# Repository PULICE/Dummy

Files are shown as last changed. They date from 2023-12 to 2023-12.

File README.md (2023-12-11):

# Dummy
稚晖君dummy复制，目标是全国产谐波减速器本仓库继承自https://gitee.com/switchpi/dummy.git

1. 目录描述
- Firmware 包括ref控制板，42，35驱动板所用源代码
- Hardware 重新设计包括ref控制板，42，35驱动板schematic, pcb所有文件
- 3d-model 所有复制dummy 3d打印文件
- ESP32-iot esp32 supports files

1. 重新设计的ref控制板
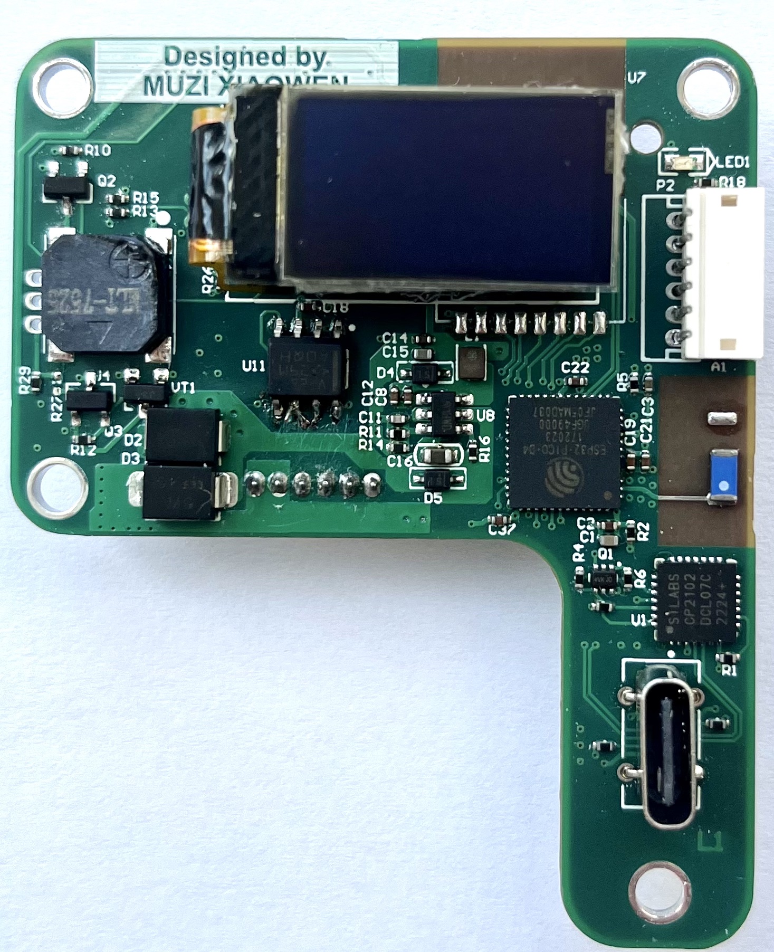
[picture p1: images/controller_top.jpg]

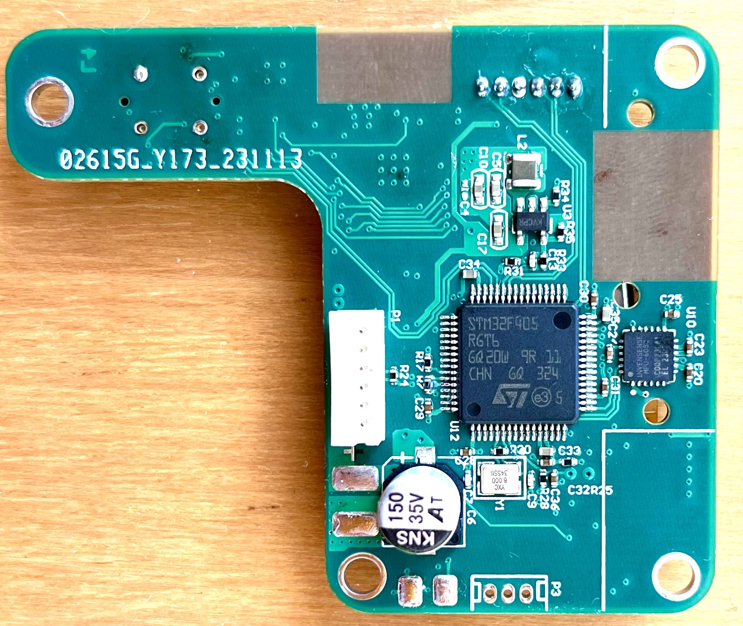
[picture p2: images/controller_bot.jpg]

- 简化设计，更适合量产
1. 修改所有1.0mm的连接器为插针1.5mm，fix原版连接器容易脱落
1. 删除base板，将base板子集成到了主板上
1. 添加switching ldo，供电电流最大2A，fix原版mcu ldo电流过小，温度过高issue
1. 将led ring，buzzer 控制从ESP32 改到stm32 mcu
1. 更合理的布局
1. 降低量产成本

1. 重新设计的42/35驱动板

- 42/35驱动板正式版
1. 所有连接器改为1.5mm 3A 座子，更适合量产
1. 电源线复用两根1007/26号线，最大支持到3A
1. CAN BUS ID 通过板载拨码开关设置

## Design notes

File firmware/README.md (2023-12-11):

--原理图基于并且拥有者稚晖君，原理图修改版和PCB设计木子晓文。--

Based on ZhiHuiJun schematic, the oringal design owned by ZhiHuiJun. Schematic modified and PCB designed by Muzi Xiaowen. 
The schematic and PCB design are free and open, and comes with ABSOLUTELY NO WARRANTY, to the extent permitted by applicable law.

References
https://github.com/peng-zhihui/Dummy-Robot

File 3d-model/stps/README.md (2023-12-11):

### step 3d models
- Thanks to PULI @pu_li_ce 
- Refer to Fan-feature branch

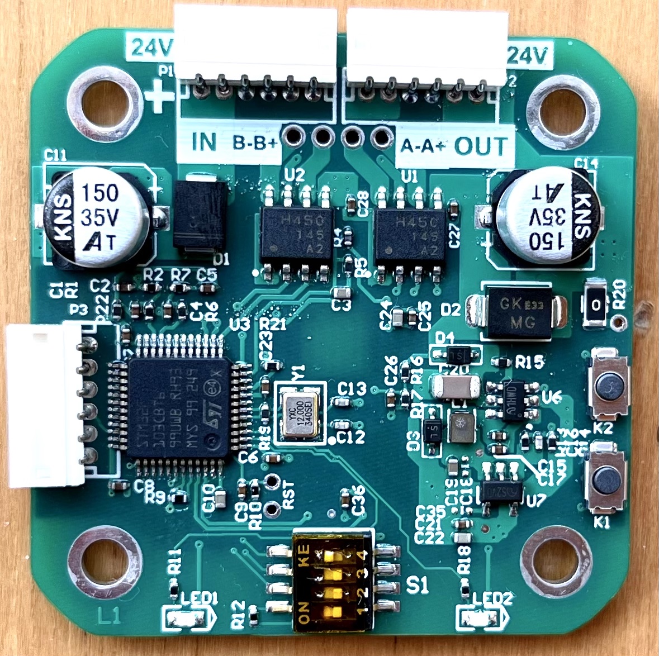
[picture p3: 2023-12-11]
images/m42.jpg

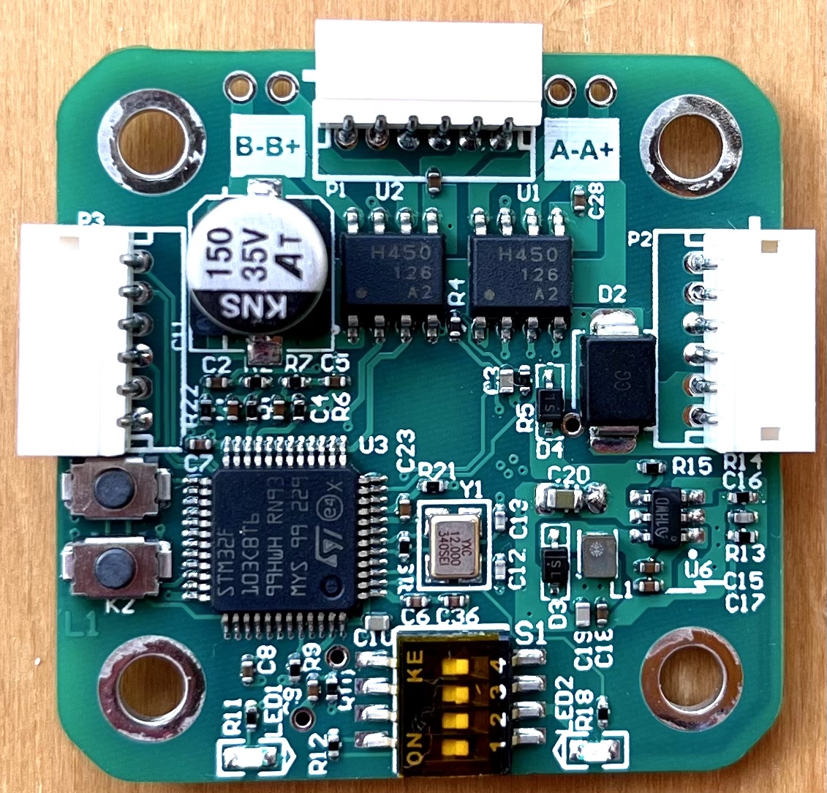
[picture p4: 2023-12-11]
images/m35.jpg

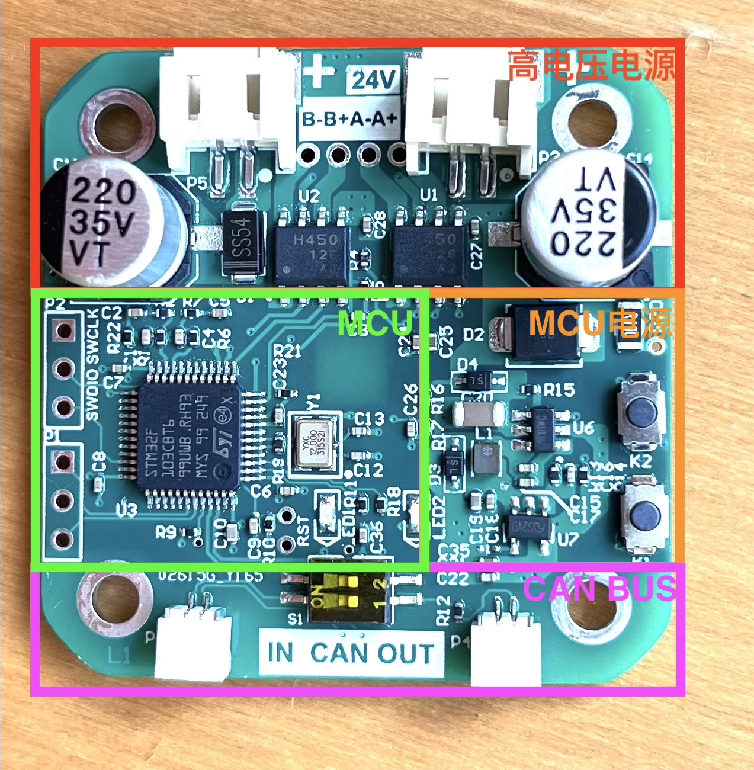
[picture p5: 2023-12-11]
images/top.jpg

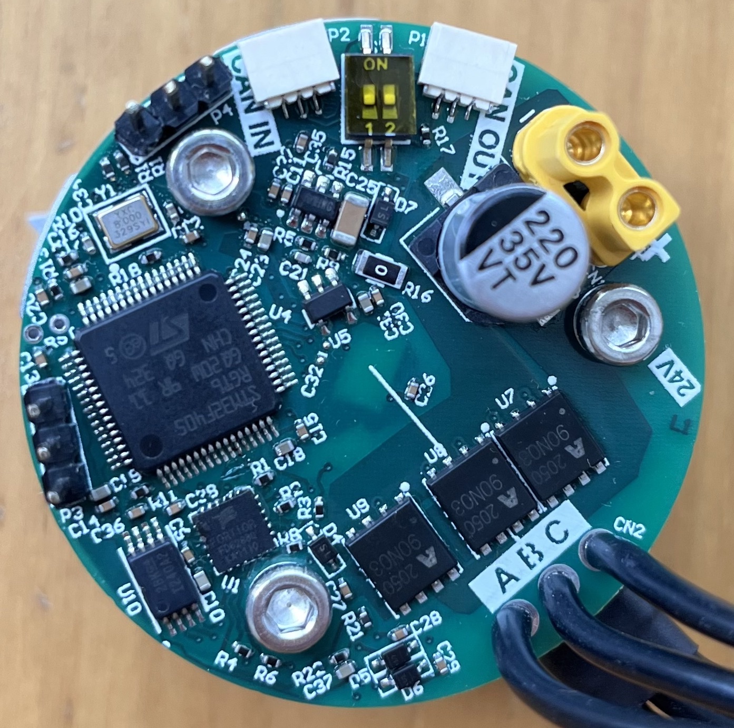
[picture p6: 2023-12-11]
images/bldc.jpg

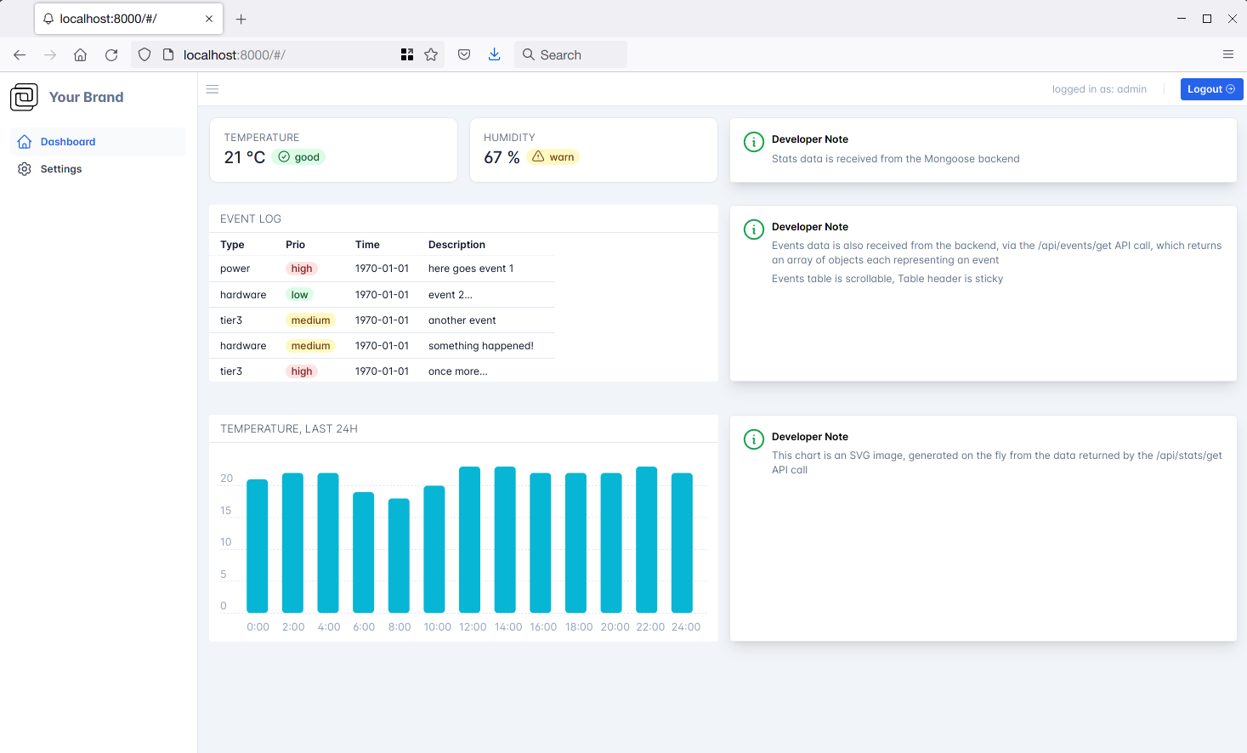
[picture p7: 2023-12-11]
esp32-iot/firmware/examples/device-dashboard/screenshots/dashboard.webp

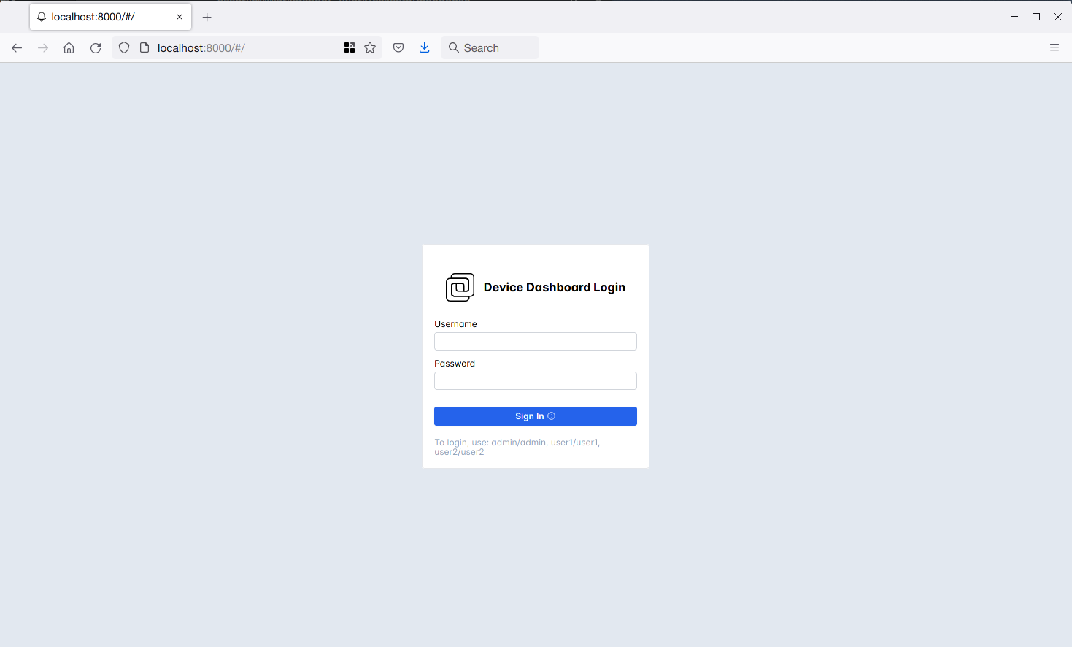
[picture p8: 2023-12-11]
esp32-iot/firmware/examples/device-dashboard/screenshots/login.webp

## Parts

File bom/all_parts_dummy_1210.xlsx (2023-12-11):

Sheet: Motor-42
Comment | Description | Designator | Footprint | LibRef | Quantity
0.1uF | Capacitor | C1, C2, C4, C5, C6, C7, C8, C9, C15, C17, C18, C21, C25, C26 | CAP_0402 | 电容-0402 | 14
10uF | Capacitor | C3, C10, C19, C22, C24 | CAP_0402 | 电容-0402 | 5
100uF | Capacitor | C11, C12, C13, C14 | 1206-CAP | 电容-1206 | 4
100pF | Capacitor | C16 | CAP_0402 | 电容-0402 | 1
10uF/50V | Capacitor | C20 | CAP_0402 | 电容-0402 | 1
10nF | Capacitor | C23 | CAP_0402 | 电容-0402 | 1
SS54 | Diode | D1 | DO-214AC | Diode_SMA | 1
SMBJ28CA |  | D2 | SMBJ-CA_MFG | SMBJ28CA | 1
二极管-5819W | 40V | D3, D4 | SOD-323 | 二极管-5819W | 2
跳线 | Resistor | J1 | 0402-0R | 跳线 | 1
TACT 2P | Button | K1, K2 | ButtonTACT_3x4x2_180 | ButtonTACT_3x4x2_180 | 2
6.8uH |  | L1 | IND-201612 | 电感-201612 | 1
SH1.0-5P |  | P1 | SH1.0-5P | SH1.0-5P | 1
SH1.0-6P |  | P2, P3, P4 | SH1.0-6P | SH1.0-6P | 3
SH1.0-3P | Header | P5 | SH1.0-3P | SH1.0-3P | 1
1K | Resistor | R1, R2, R6, R7, R17 | RES_0402 | 电阻-0402 | 5
0.1R | Resistor | R3, R8 | 1206-RES | 电阻-1206 | 2
NCP15XH103F03RC | THERMISTOR 10K OHM NTC 0402 SMD | R4 | RES_0402 | NCP15XH103F03RC | 1
3.3K | Resistor | R5 | RES_0402 | 电阻-0402 | 1
10K | Resistor | R9, R10, R13, R16 | RES_0402 | 电阻-0402 | 4
120R | Resistor | R11, R12 | RES_0402 | 电阻-0402 | 2
1.8K | Resistor | R14 | RES_0402 | 电阻-0402 | 1
1M | Resistor | R15 | RES_0402 | 电阻-0402 | 1
测试点 |  | T1, T2 | TEST_PT | 测试点 | 2
TB67H450FNG | PWM Chopper Type DC Brushed Motor Driver | U1, U2 | SO-8-PAD | TB67H450FNG | 2
STM32F103CBT6 | ARM Cortex-M3 32-bit MCU, 128 KB Flash, 20 KB Internal RAM, 37 I/Os, 48-pin LQFP, -40 to 85 degC, Tray | U3 | LQFP-48 | STM32F103CBT6 | 1
TL431IDBZT | Adjustable precision shunt regulator 3-SOT-23 -40 to 85 | U4 | SOT23-3 | TL431IDBZT | 1 | taobao
SN65HVD232D |  | U5 | SO-8 | SN65HVD232D | 1
ME3116 | DC-DC | U6 | SOT23-6 | ME3116 | 1
LP2992 3V3 | LDO | U7 | SOT23-5 | LP2992 | 1
MT6816 | Magnetic Position Sensor | U8 | SO-8 | MT6816 | 1
12MHz | 村田贴片 | Y1 | 晶振-3P | 晶振-3Pin | 1 | taobao

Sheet: Motor-20
Comment | Description | Designator | Footprint | LibRef | Quantity
0.1uF | Capacitor | C1, C2, C3, C4, C5, C6, C7, C8, C11, C15, C16, C20, C21 | CAP_0402 | 电容-0402 | 13
100uF | Capacitor | C9, C10 | 1206-CAP | 电容-1206 | 2
10uF | Capacitor | C12, C17, C18, C19 | CAP_0402 | 电容-0402 | 4
10nF | Capacitor | C13 | CAP_0402 | 电容-0402 | 1
100pF | Capacitor | C14 | CAP_0402 | 电容-0402 | 1
SS54 | Diode | D1 | DO-214AC | Diode_SMA | 1
SMBJ28CA |  | D2 | SMBJ-CA_MFG | SMBJ28CA | 1
二极管-5819W | 40V | D3, D4 | SOD-323 | 二极管-5819W | 2
跳线 | Resistor | J1 | 0402-0R | 跳线 | 1
TACT 2P | Button | K1, K2 | ButtonTACT_3x4x2_180 | ButtonTACT_3x4x2_180 | 2
6.8uH |  | L1 | IND-201612 | 电感-201612 | 1
SH1.0-2P |  | P1, P2 | SH1.0-2P | SH1.0-2P | 2
SH1.0-3P | Header | P3 | SH1.0-3P | SH1.0-3P | 1
1K | Resistor | R1, R2, R4, R5, R14 | RES_0402 | 电阻-0402 | 5
0.1R | Resistor | R3, R6 | 1206-RES | 电阻-1206 | 2
10K | Resistor | R7, R8, R10, R13 | RES_0402 | 电阻-0402 | 4
120R | Resistor | R9 | RES_0402 | 电阻-0402 | 1
1.8K | Resistor | R11 | RES_0402 | 电阻-0402 | 1
1M | Resistor | R12 | RES_0402 | 电阻-0402 | 1
TB67H450FNG | PWM Chopper Type DC Brushed Motor Driver | U1, U2 | SO-8-PAD | TB67H450FNG | 2
STM32F103CBT6 | ARM Cortex-M3 32-bit MCU, 128 KB Flash, 20 KB Internal RAM, 37 I/Os, 48-pin LQFP, -40 to 85 degC, Tray | U3 | LQFP-48 | STM32F103CBT6 | 1
SN65HVD232D |  | U4 | SO-8 | SN65HVD232D | 1
LP2992 3V3 | LDO | U5 | SOT23-5 | LP2992 | 1
ME3116 | DC-DC | U6 | SOT23-6 | ME3116 | 1
MT6816 | Magnetic Position Sensor | U7 | SO-8 | MT6816 | 1
12MHz | 村田贴片 | Y1 | 晶振-3P | 晶振-3Pin | 1 | taobao

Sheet: REF-UNIT
Comment | Description | Designator | Footprint | LibRef | Quantity
OLED-12880 |  | 1 | OLED-12880 | OLED-12880 | 1
0.1uF | Capacitor | C1, C6, C7, C9, C12, C13, C14, C15, C16, C20 | CAP_0402 | 电容-0402 | 10
10uF | Capacitor | C2, C5, C10, C11, C17, C18, C19 | CAP_0402 | 电容-0402 | 7
10nF | Capacitor | C3, C4 | CAP_0402 | 电容-0402 | 2
2.2nF | Capacitor | C8 | CAP_0402 | 电容-0402 | 1
color? | LED | D1 | LED_0402_RED | LED_0402 | 1
B2B-Connector-28P-0.5mm |  | J1, J2 | B2B-0.5mm-28P-M | B2B-Connector-28P-0.5mm | 2
2K | Resistor | R1, R2, R3 | RES_0402 | 电阻-0402 | 3
4.7K | Resistor | R4, R5, R8 | RES_0402 | 电阻-0402 | 3
10K | Resistor | R6, R13 | RES_0402 | 电阻-0402 | 2
560K | Resistor | R7 | RES_0402 | 电阻-0402 | 1
120R/NC | Resistor | R9 | RES_0402 | 电阻-0402 | 1
0R | Resistor | R10, R11 | RES_0402 | 电阻-0402 | 2
22R | Resistor | R12, R14 | RES_0402 | 电阻-0402 | 2
LP2992 3V3 | LDO | U1 | SOT23-5 | LP2992 | 1
MPU6050 | 六轴传感器 | U2 | QFN-24 | MPU6050 | 1
SN65HVD232D |  | U3 | SO-8 | SN65HVD232D | 1
STM32F405RGT6 | ARM Cortex-M4 32-bit MCU+FPU, 210 DMIPS, 1024 kB Flash, 192 kB Internal RAM, 51 I/Os, 64-pin LQFP, -40 to 85 degC, Tray | U4 | LQFP-64_N | STM32F405RGT6 | 1
8MHz | 村田贴片 | Y1 | 晶振-3P | 晶振-3Pin | 1 | taobao

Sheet: REF-Base
Comment | Description | Designator | Footprint | LibRef | Quantity
RAINSUN |  | A1 | ANT-Rainsun-AN5120 | ANT-Rainsun-AP5120 | 1
10uF | Capacitor | C1, C5, C10, C15 | CAP_0402 | 电容-0402 | 4
0.1uF | Capacitor | C2, C4, C8, C9, C12, C14 | CAP_0402 | 电容-0402 | 6
1uF | Capacitor | C3 | CAP_0402 | 电容-0402 | 1
100uF | Capacitor | C6 | 1206-CAP | 电容-1206 | 1 | 22uF/35V
10nF | Capacitor | C7, C13 | CAP_0402 | 电容-0402 | 2
100pF | Capacitor | C11 | CAP_0402 | 电容-0402 | 1
10uF/50V | Capacitor | C16 | CAP_0402 | 电容-0402 | 1 | 2.2uF/35V
color? | LED | D1 | LED_0402_RED | LED_0402 | 1
SS54 | Diode | D2 | DO-214AC | Diode_SMA | 1
SMBJ28CA |  | D3 | SMBJ-CA_MFG | SMBJ28CA | 1
二极管-5819W | 40V | D4, D5 | SOD-323 | 二极管-5819W | 2
USB-TYPE-C-STAND |  | J1 | USB-TYPE-C-STAND | USB-TYPE-C-STAND | 1
6.8uH |  | L1 | IND-201612 | 电感-201612 | 1
SH1.0-5P |  | P1 | SH1.0-5P | SH1.0-5P | 1
SH1.0-2P |  | P2, P3, P4 | SH1.0-2P | SH1.0-2P | 3
SH1.0-3P | Header | P5, P6 | SH1.0-3P | SH1.0-3P | 2
BC847BVC-7 |  | Q1 | SOT563-6 | BC847BVC-7 | 1
AO3400A | N-MOS | Q2 | SOT23-3 | AO3400A | 1
AO3401A | P-MOS | Q3 | SOT23-3 | AO3401A | 1
10K | Resistor | R1, R5, R10, R11, R15 | RES_0402 | 电阻-0402 | 5
0R | Resistor | R2 | RES_0402 | 电阻-0402 | 1
200R | Resistor | R3 | RES_0402 | 电阻-0402 | 1
12K | Resistor | R4, R6 | RES_0402 | 电阻-0402 | 2
2K | Resistor | R7, R12 | RES_0402 | 电阻-0402 | 2
5.1K | Resistor | R8, R9 | RES_0402 | 电阻-0402 | 2
1K | Resistor | R13 | RES_0402 | 电阻-0402 | 1
1.8K | Resistor | R14 | RES_0402 | 电阻-0402 | 1
1M | Resistor | R16 | RES_0402 | 电阻-0402 | 1
REF-Unit | Robot Embedded Framework based on STM43F405RGT6. | S1 | REF-UNIT | REF-Unit | 1
CP2102 | USB转TTL | U1 | QFN-28 | CP2102 | 1
ESP32_SIP |  | U2 | QFN-48_7X7 | ESP32-PICO | 1
LP2992 3V3 | LDO | U3, U6 | SOT23-5 | LP2992 | 2
DET402 |  | U4 | DET402 | DET402 | 1
SN65HVD232D |  | U5 | SO-8 | SN65HVD232D | 1
NRF24L01 |  | U7 | NRF24L01-MODULE | NRF24L01模块 | 1
ME3116 | DC-DC | U8 | SOT23-6 | ME3116 | 1
S8050 | Surface mount NPN transistor, package SOT-23 | VT1 | SMT_TRIODE_NPN | SMT_TRIODE_NPN | 1

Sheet: screws
 |  | 数量
J1
M4*21mm |  | 2
M4*12MM | mini11 减速器到base外壳 | 2
M3*34MM | 42电机 | 4
M3*5MM | mini11 减速器适配件固定到42电机 | 2
M3*20MM | j1 固定到外壳 | 6
M3*18MM | j1 连杆固定到j2减速器 | 3
固定底座
M3*28MM | 固定到底座 | 4
J2/J3
M3*25 | 固定j2/j3减速器适配件 | 4
M3*30 | 固定j2/j3减速器到连杆 | 4
M3*15 | 固定j2 42 Motor到连杆 | 4
M3*42 | 固定3个 42 Motor 驱动板 | 12
M3*11MM | 固定j3 42 Motor到连杆 | 4
Joint4
M3*6MM | 固定j4 35 Motor到连杆 | 4
M3*13MM | 固定3个 35 Motor 驱动板 | 12
M3*13Mm | 固定j4减速器到连杆 | 3
Joint5
M3*8MM | 固定2个 35 Motor 到连杆 | 4
M3*19MM | 固定j5减速器到连杆 | 1

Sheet: 3d
 |  | 数量
Base.stl | joint1底座 | 1
joint23.stl | joint23联杆 | 1
joint4.stl | joint4联杆 | 1
joint5.stl | joint5联杆 | 1
joint6.stl | joint6联杆 | 1
mini11-bracket-metal.stl | mini11与42电机连接支架 | 1
mini8-bracket-metal.stl | mini8谐波连接支架 | 4
motor42-bracket-top-metal.stl | 42驱动板散热顶盖 | 3
motor35-bracket-top-metal.stl | 35驱动板散热顶盖 | 2

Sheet: parts
42电机驱动板 |  | 3 | b站 木子晓汶 工房
35电机驱动板 |  | 3 | b站 木子晓汶 工房
42 电机 | l=40 1a | 3 | https://item.taobao.com/item.htm?id=549501040122&ns=1&abbucket=13
35 电机 | l=28 1a | 3 | https://item.taobao.com/item.htm?spm=a1z09.2.0.0.17872e8dTWSTmP&id=15168111895&_u=83jnrl7aaaff
减速器 | mini11 | 1 | taobao
减速器 | mini8 | 5 | taobao
同步轮 | 20齿内孔5mm外径18 | 8 | https://item.taobao.com/item.htm?spm=a1z09.2.0.0.19b12e8dfRIPU3&id=625483500699&_u=a3jnrl7adc93
同步皮带 | 152mm | 1 | https://item.taobao.com/item.htm?spm=a1z09.2.0.0.19b12e8dfRIPU3&id=626759355655&_u=a3jnrl7aa476
同步皮带 | 120mm | 1 | https://item.taobao.com/item.htm?spm=a1z09.2.0.0.19b12e8dfRIPU3&id=626759355655&_u=a3jnrl7aa476
同步皮带 | 110mm | 1 | https://item.taobao.com/item.htm?spm=a1z09.2.0.0.19b12e8dfRIPU3&id=626759355655&_u=a3jnrl7aa476
同步皮带 | 184mm | 1 | https://item.taobao.com/item.htm?spm=a1z09.2.0.0.19b12e8dfRIPU3&id=626759355655&_u=a3jnrl7aa476
电源开关 | 开孔直径：16mm，12-24v | 1 | https://item.taobao.com/item.htm?spm=a1z09.2.0.0.6dcd2e8dgKFAl1&id=589544046782&_u=93jnrl7aceb2
DC电源插座 | DC5.5*2.5mm | 1 | https://item.taobao.com/item.htm?spm=a1z09.2.0.0.6dcd2e8dgKFAl1&id=679108658727&_u=93jnrl7a3b6f
电源 | 24v 6a | 1 | https://item.taobao.com/item.htm?spm=a1z09.2.0.0.6dcd2e8dgKFAl1&id=552809889509&_u=93jnrl7a25cd
6pin排线 | zh1.5mm 30CM(定做) | 1 | https://detail.tmall.com/item.htm?_u=93jnrl7a54c7&id=642559605753&spm=a1z09.2.0.0.6dcd2e8dgKFAl1
6pin排线 | zh1.5mm 20CM(定做) | 6 | https://detail.tmall.com/item.htm?_u=93jnrl7a54c7&id=642559605753&spm=a1z09.2.0.0.6dcd2e8dgKFAl1

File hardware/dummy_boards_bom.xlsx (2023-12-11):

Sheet: REF
Comment | Quantity | Designator | Footprint | Layer
0R | 4 | R2, R26, R27, R29 | RES_0402_1 | Top
0.1uF | 9 | C2, C8, C12, C14, C18, C19, C21, C22, C37 | CAP_0402 | Top
1K | 1 | R13 | RES_0402_1 | Top
1M | 1 | R16 | RES_0402_1 | Top
1uF | 1 | C3 | CAP_0402 | Top
1.8K | 1 | R14 | RES_0402_1 | Top
2K | 2 | R12, R18 | RES_0402_1 | Top
4.7K | 3 | R19, R20, R23 | RES_0402_1 | Top
4.7uF | 1 | C16 | C0603 | Top
5.1K | 2 | R8, R9 | RES_0402_1 | Top
6.8uH | 1 | L1 | IND-201612 | Top
10K | 6 | R1, R5, R10, R11, R15, R21 | RES_0402_1 | Top
10uF | 4 | C1, C15, C26, C27 | CAP_0402 | Top
12K | 2 | R4, R6 | RES_0402_1 | Top
100pF | 1 | C11 | CAP_0402 | Top
200R | 1 | R3 | RES_0402_1 | Top
560K | 1 | R22 | RES_0402_1 | Top
AO3400A | 1 | Q2 | SOT23-3 | Top
AO3401A | 1 | Q3 | SOT23-3 | Top
BC847BVC-7 | 1 | Q1 | SOT563-6 | Top
CP2102 | 1 | U1 | QFN-28 | Top
ESP32_SIP | 1 | U2 | QFN-48_7X7 | Top
Header 6H | 1 | P2 | CONN-TH_HC-ZH1.5-6A-s | Top
LED GREEN | 1 | LED1 | LED-0603 | Top
ME3116 | 1 | U8 | SOT23-6 | Top
MLT-7525 | 1 | U4 | BUZ-SMD_4P-L7.5-W7.5-P7.59-TL | Top
NRF24L01 | 1 | U7 | NRF24L01-MODULE | Top
OLED-12880 | 1 | 1 | OLED-12880 | Top
RAINSUN | 1 | A1 | ANT-Rainsun-AN5120 | Top
S8050 | 1 | VT1 | SMT_TRIODE_NPN | Top
SMBJ28CA | 1 | D3 | SMBJ-CA_MFG | Top
SN65HVD232D | 1 | U11 | SO-8 | Top
SS54 | 1 | D2 | DO-214AC | Top
USB-TYPE-C-STAND | 1 | J1 | USB-TYPE-C-STAND | Top
b5819W | 2 | D4, D5 | SOD-323 | Top
0R | 2 | R25, R31 | RES_0402_1 | Bottom
0.1uF | 10 | C4, C20, C23, C25, C28, C29, C30, C31, C32, C36 | CAP_0402 | Bottom
1M | 1 | R30 | RES_0402 | Bottom
2K | 2 | R7, R17 | RES_0402_1 | Bottom
2.2nF | 1 | C24 | CAP_0402 | Bottom
2.2uH | 1 | L2 | IND-252012A-2R2 | Bottom
10K | 2 | R28, R34 | RES_0402_1 | Bottom
10uF | 3 | C33, C34, C35 | CAP_0402 | Bottom
20pF | 2 | C7, C9 | CAP_0402 | Bottom
20pF | 1 | C13 | CAP_0402 | Bottom
22uF | 3 | C5, C10, C17 | C0603 | Bottom
22.1K | 1 | R35 | RES_0402_1 | Bottom
100K | 1 | R33 | RES_0402_1 | Bottom
120R/NC | 1 | R24 | RES_0402_1 | Bottom
220uF/25V | 1 | C6 | CAP-SMD_BD8.0-L8.3-W8.3-LS9.3-FD | Bottom
Header 3 | 1 | P3 | CONN-TH_HC-ZH1.5-3A-S | Bottom
Header 6H | 1 | P1 | CONN-TH_HC-ZH1.5-6A | Bottom
MPU6050 | 1 | U10 | QFN-24 | Bottom
STM32F405RGT6 | 1 | U12 | LQFP-64_N | Bottom
SY8089 2A | 1 | U3 | SOT23-5 | Bottom
XTAL-4 | 1 | Y1 | LC-SMD-3225_4P | Bottom

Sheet: Motor-42
Comment | Description | Designator | Footprint | Quantity | Layer
0.1R | Resistor | R3, R8 | 1206-RES | 2 | Bottom
10uF/50V | Capacitor, chip, ceramic | C29, C30, C31, C32, C33, C34 | 1206-CAP | 6 | Bottom
MT6816 | Magnetic Position Sensor | U8 | SO-8 | 1 | Bottom
SN65HVD232D |  | U5 | so-8 | 1 | Bottom
0 | Resistor | R21, R22 | RES_0402 | 2 | Top
0R | Resistor | R20 | 1206-RES | 1 | Top
0.1uF | Capacitor | C1, C2, C4, C5, C6, C7, C8, C9, C15, C17, C18, C21, C23, C25, C26, C27, C28, C35, C36 | CAP_0402 | 19 | Top
1K | Resistor | R1, R2, R6, R7, R11, R17, R18 | RES_0402 | 7 | Top
1M | Resistor | R15, R19 | RES_0402 | 2 | Top
1.8K | Resistor | R14 | RES_0402 | 1 | Top
3.3K | Resistor | R5 | RES_0402 | 1 | Top
6.8uH |  | L1 | IND-201612 | 1 | Top
10K | Resistor | R9, R10, R13, R16 | RES_0402 | 4 | Top
10uF | Capacitor | C3, C10, C19, C22, C24 | CAP_0402 | 5 | Top
10uF/50V | Capacitor | C20 | 1206-CAP | 1 | Top
20pF | Capacitor | C12, C13 | CAP_0402 | 2 | Top
100pF | Capacitor | C16 | CAP_0402 | 1 | Top
120R | Resistor | R12 | RES_0402 | 1 | Top
220uF/25V | Capacitor, chip, ceramic | C11, C14 | CAP-SMD_BD8.0-L8.3-W8.3-LS9.3-FD | 2 | Top
DSHP04TSGER | DIP Switches / SIP Switches 4 pos. low profile Btm Seal Tape J Bend | S1 | SW-SMD_DSHP04TS-S | 1 | Top
Header 6H | Header, 6-Pin, Right Angle | P1, P2, P3 | CONN-TH_HC-ZH1.5-6A-s | 3 | Top
LED GREEN | LED GRN SGL RA 25mA 4.1V SMD | LED1, LED2 | LED-0603 | 2 | Top
LP2992 3V3 | LDO | U7 | SOT23-5 | 1 | Top
ME3116 | DC-DC | U6 | SOT23-6 | 1 | Top
NCP15XH103F03RC | THERMISTOR 10K OHM NTC 0402 SMD | R4 | RES_0402 | 1 | Top
SMBJ28CA |  | D2 | SMBJ-CA_MFG | 1 | Top
SS54 | Diode | D1 | DO-214AC | 1 | Top
STM32F103CBT6 | ARM Cortex-M3 32-bit MCU, 128 KB Flash, 20 KB Internal RAM, 37 I/Os, 48-pin LQFP, -40 to 85 degC, Tray | U3 | LQFP-48 | 1 | Top
TACT 2P | Button | K1, K2 | ButtonTACT_3x4x2_180 | 2 | Top
TB67H450FNG | PWM Chopper Type DC Brushed Motor Driver | U1, U2 | SO-8-PAD | 2 | Top
XTAL-4 | Crystal | Y1 | LC-SMD-3225_4P | 1 | Top
二极管-5819W | 40V | D3, D4 | SOD-323 | 2 | Top

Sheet: Motor-35
Comment | Quantity | Description | Designator | Footprint | Layer
0R | 1 | Resistor | R20 | 1206-RES | Bottom
0.1R | 2 | Resistor | R3, R8 | 1206-RES | Bottom
0.1uF | 2 | Capacitor | C21, C25 | CAP_0402 | Bottom
10uF | 2 | Capacitor | C22, C24 | CAP_0402 | Bottom
10uF/50V | 4 | Capacitor, chip, ceramic | C29, C30, C31, C32 | 1206-CAP | Bottom
LP2992 3V3 | 1 | LDO | U7 | SOT23-5 | Bottom
MT6816 | 1 | Magnetic Position Sensor | U8 | SO-8 | Bottom
SN65HVD232D | 1 |  | U5 | so-8 | Bottom
SS54 | 1 | Diode | D1 | DO-214AC | Bottom
0 | 2 | Resistor | R21, R22 | RES_0402 | Top
0.1uF | 15 | Capacitor | C1, C2, C4, C5, C6, C7, C8, C9, C15, C17, C18, C23, C27, C28, C36 | CAP_0402 | Top
1K | 6 | Resistor | R1, R2, R6, R7, R11, R18 | RES_0402 | Top
1M | 2 | Resistor | R15, R19 | RES_0402 | Top
1.8K | 1 | Resistor | R14 | RES_0402 | Top
3.3K | 1 | Resistor | R5 | RES_0402 | Top
6.8uH | 1 |  | L1 | IND-201612 | Top
10K | 3 | Resistor | R9, R10, R13 | RES_0402 | Top
10uF | 3 | Capacitor | C3, C10, C19 | CAP_0402 | Top
10uF/50V | 1 | Capacitor | C20 | 1206-CAP | Top
20pF | 2 | Capacitor | C12, C13 | CAP_0402 | Top
100pF | 1 | Capacitor | C16 | CAP_0402 | Top
120R | 1 | Resistor | R12 | RES_0402 | Top
220uF/25V | 1 | Capacitor, chip, ceramic | C11 | CAP-SMD_BD8.0-L8.3-W8.3-LS9.3-FD | Top
DSHP04TSGER | 1 | DIP Switches / SIP Switches 4 pos. low profile Btm Seal Tape J Bend | S1 | SW-SMD_DSHP04TS-S | Top
Header 6H | 3 | Header, 6-Pin, Right Angle | P1, P2, P3 | CONN-TH_HC-ZH1.5-6A-s | Top
LED GREEN | 2 | LED GRN SGL RA 25mA 4.1V SMD | LED1, LED2 | LED-0603 | Top
ME3116 | 1 | DC-DC | U6 | SOT23-6 | Top
NCP15XH103F03RC | 1 | THERMISTOR 10K OHM NTC 0402 SMD | R4 | RES_0402 | Top
SMBJ28CA | 1 |  | D2 | SMBJ-CA_MFG | Top
STM32F103CBT6 | 1 | ARM Cortex-M3 32-bit MCU, 128 KB Flash, 20 KB Internal RAM, 37 I/Os, 48-pin LQFP, -40 to 85 degC, Tray | U3 | LQFP-48 | Top
TACT 2P | 2 | Button | K1, K2 | ButtonTACT_3x4x2_180 | Top
TB67H450FNG | 2 | PWM Chopper Type DC Brushed Motor Driver | U1, U2 | SO-8-PAD | Top
XTAL-4 | 1 | Crystal | Y1 | LC-SMD-3225_4P | Top
二极管-5819W | 2 | 40V | D3, D4 | SOD-323 | Top

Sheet: Screws
J1/BASE
M2*10 | 2 | fixs to controller enclosure
M3*20 | 4 | fixs to ground board
M4*20 | 2 | base to MINI11 reducer
M4*12 | 2 | MINI11 reducer bracket
M3*5 | 3 | for REF board fixs to base, flat header
M3*5 | 2 | MINI11 reducer bracket
M3*20 | 6 | MINI11 reducer adaptor to 42 Motor body
M3*20 | 3 | Joint1 link fixs to reducer
J2/J3
M3*25 | 16 | for all 4 mini8 reducer
M3*30 | 4 | for mini8 reducer fixs to arm
M3*15 | 4 | for 42 motor fixs to arm
M3*45 | 12 | for all 42 motor fixs to drive board
M3*12 | 4 | for j2/j3 up 42 motor fixs to arm
J4
M3*6 | 4 | for 35 motor fixs to arm
M3*12 | 12 | for all 35 motor fixs to drive board
J5
M3*8MM | 4 | for 35 motor fixs to arm
M3*19MM | 4 | for mini8 reducer fixs to arm
MINI8 Cover
M3*5 | 12
Bearing
5*10*4 | 5 | inner*outer*tall

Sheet: belts
J2 | 152MM
J3 | 120mm

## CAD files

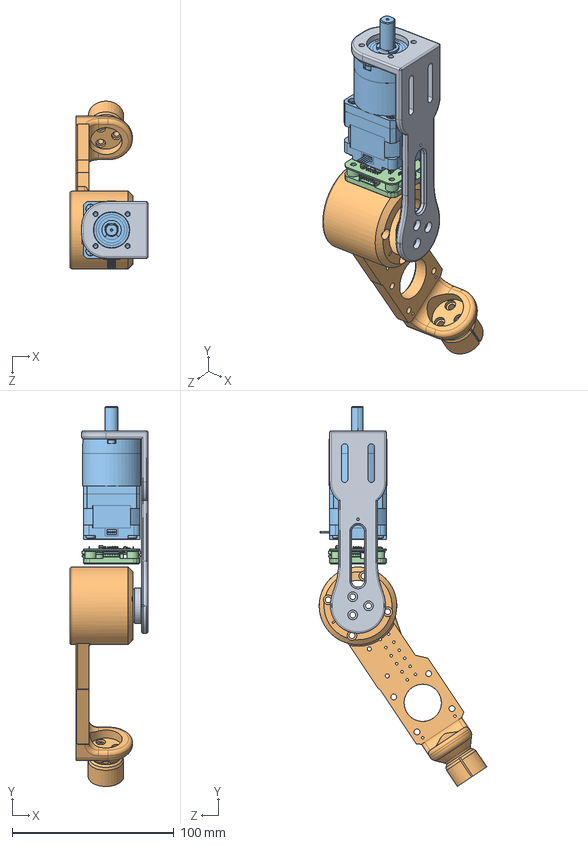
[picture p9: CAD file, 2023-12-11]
3d-model/OutStpFan/BACK/装配测试J6.SLDASM
48.2 x 234.9 x 103.6 mm
Joint6_Dummy v164 v3
Joint5_Dummy v164 v1
35HSH2408-36PG19J-300
motor35-br-top

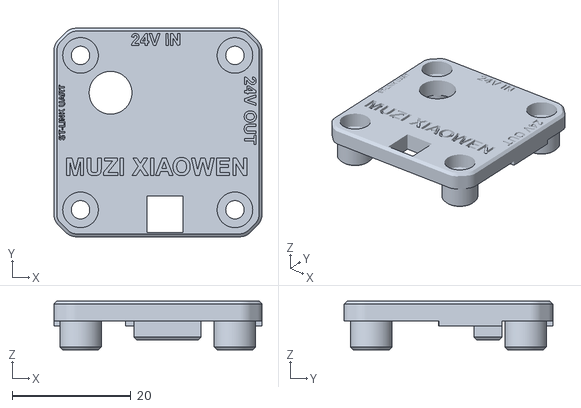
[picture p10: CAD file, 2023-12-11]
3d-model/m35/motor35-bracket-top-metal.stl
35.0 x 35.1 x 8.25

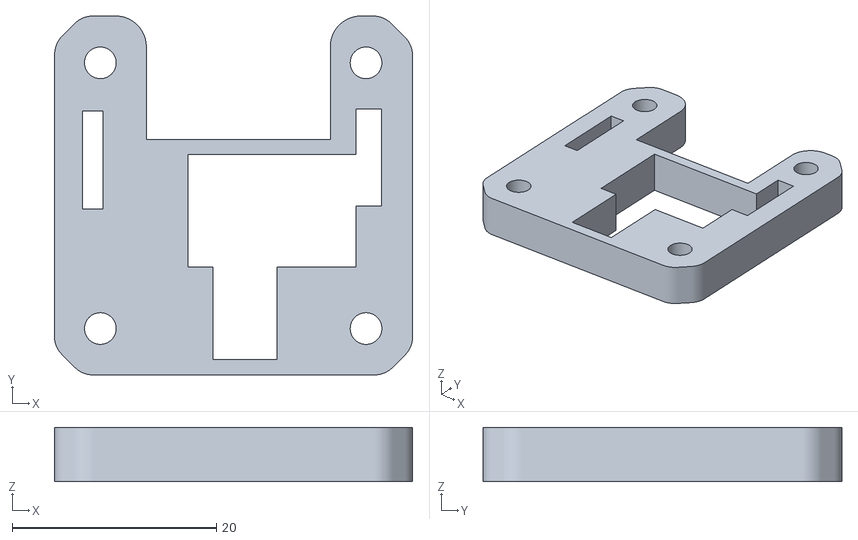
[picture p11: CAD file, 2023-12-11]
3d-model/OutStpFan/3D/m35/motor35-bracket-bot.stl
35.1 x 35.1 x 5.30

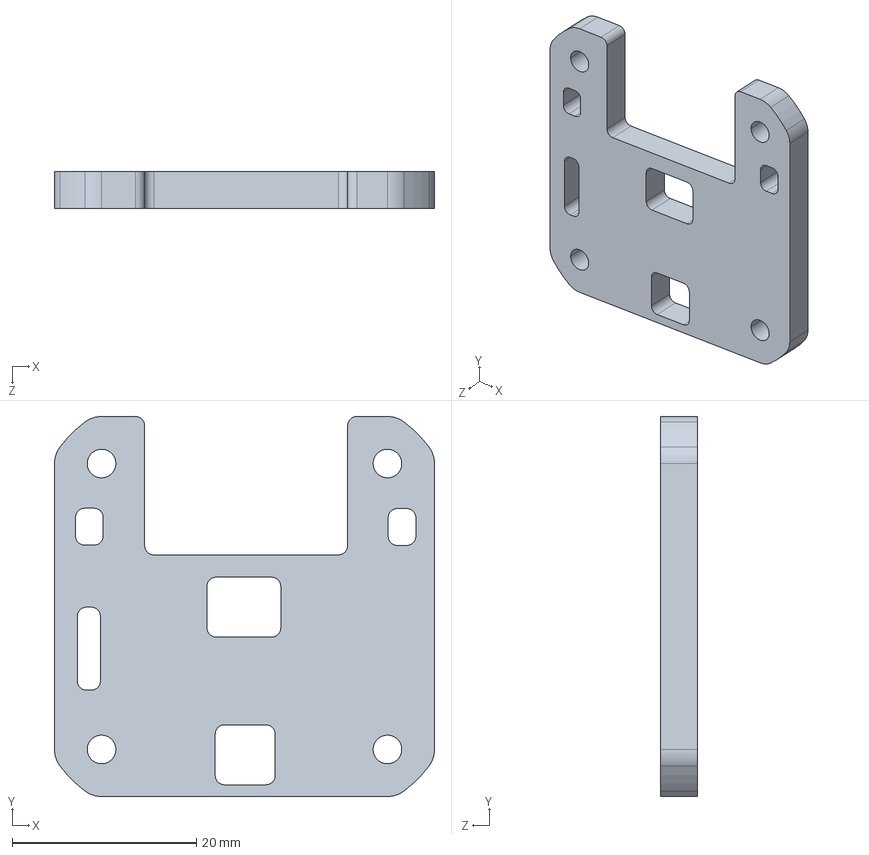
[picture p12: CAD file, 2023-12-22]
3d-model/OutStpFan/3D/m42/fan_42boot_4mm.STEP
41.2 x 41.2 x 4.00 mm

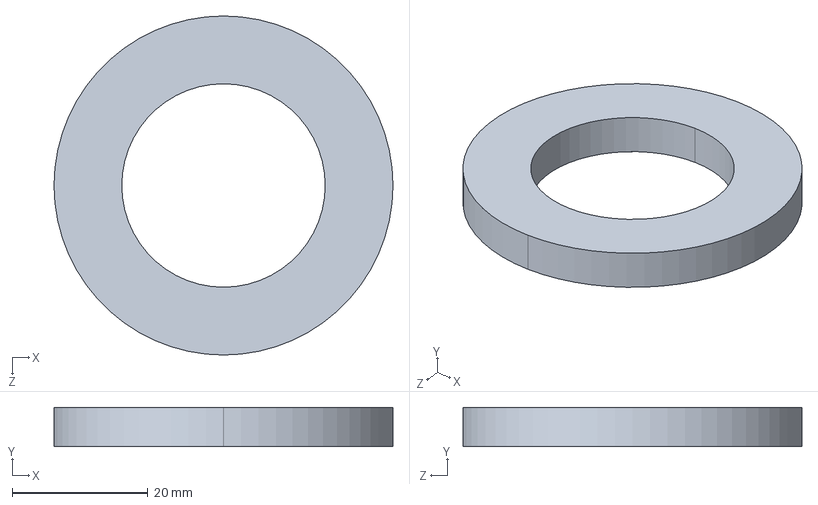
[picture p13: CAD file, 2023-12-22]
3d-model/OutStpFan/3D/YAKE_LED.STEP
50.0 x 5.80 x 50.0 mm

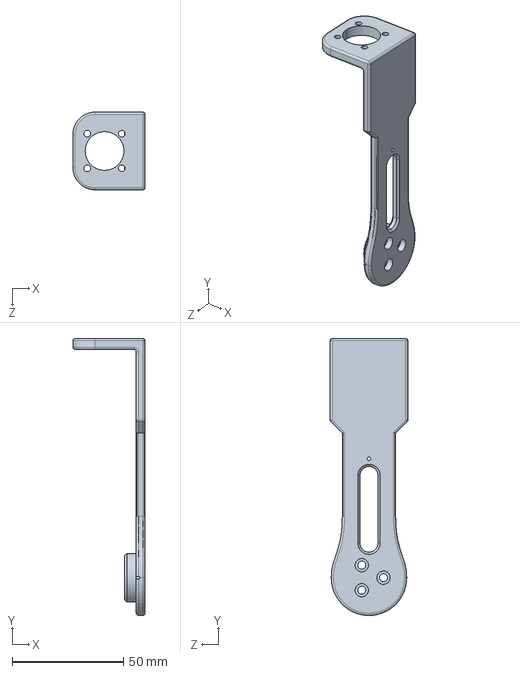
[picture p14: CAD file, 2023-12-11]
3d-model/OutStpFan/BACK/Joint6_Dummy v164 v4.STEP
32.5 x 124.6 x 35.0 mm

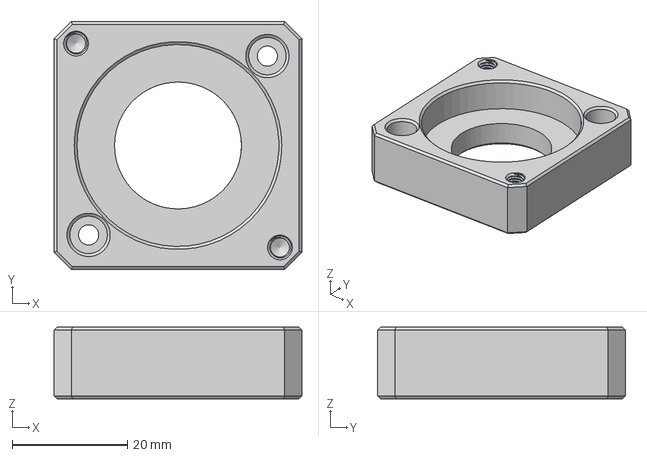
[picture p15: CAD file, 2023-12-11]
3d-model/OutStpFan/BACK/metal_step/min-11-bra-connection.step
43.0 x 43.0 x 12.4 mm

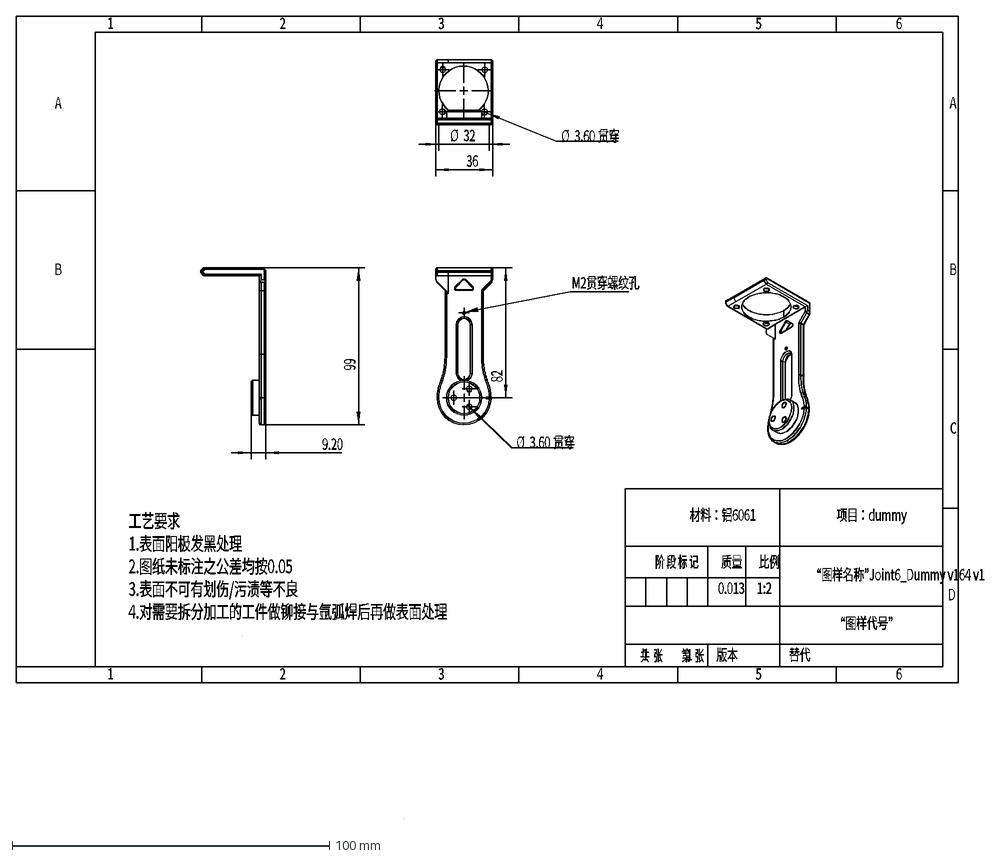
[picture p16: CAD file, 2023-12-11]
3d-model/OutStpFan/dxf/Joint6_Dummy v164 v1.DXF
替代
版本
比例
质量
第 张
共 张
阶 段 标 记
“图样代号”
“图样名称”Joint6_Dummy v164 v1
0.013
1
1:2
B
A
D
C
2
5
4
3
6
材料：铝6061
项目：dummy
工艺要求
1.表面阳极发黑处理
2.图纸未标注之公差均按0.05
3.表面不可有划伤/污渍等不良
4.对需要拆分加工的工件做铆接与氩弧焊后再做表面处理
Ø
3.60
贯穿
82
M2贯穿螺纹孔
99
9.20
36
32

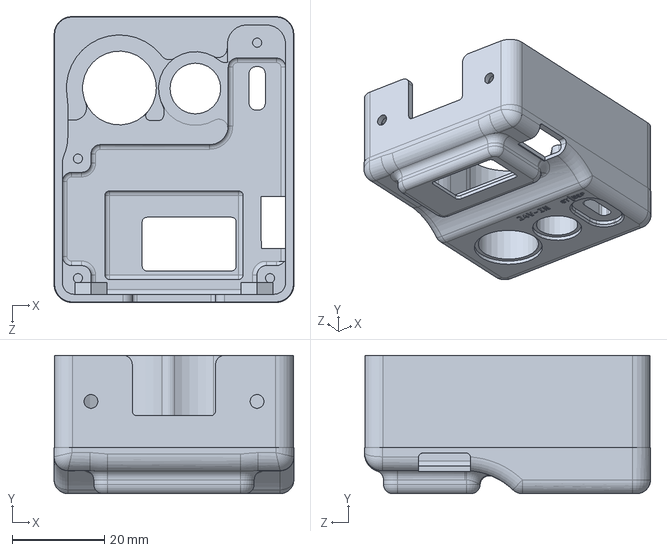
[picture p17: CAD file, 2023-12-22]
3d-model/OutStpFan/src/rfback.step.SLDPRT
52.0 x 30.0 x 62.0 mm

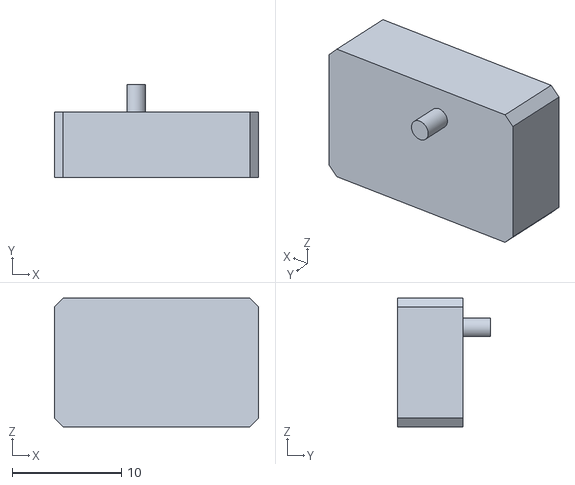
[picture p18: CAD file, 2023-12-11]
3d-model/ref-controller/contorller-oled-bracket.stl
18.7 x 8.50 x 11.8

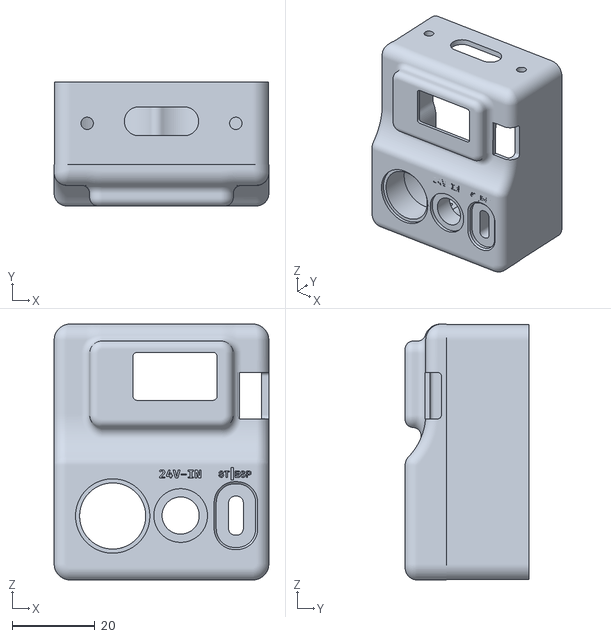
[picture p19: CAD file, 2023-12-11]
3d-model/STL/controller_enclosure.stl
52.0 x 30.0 x 62.0

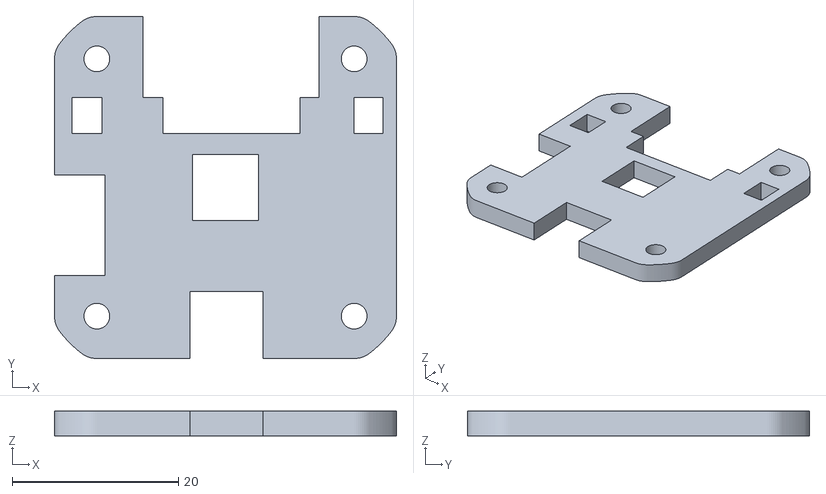
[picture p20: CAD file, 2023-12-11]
3d-model/m42/motor42-bracket-bot.stl
41.2 x 41.2 x 3.00

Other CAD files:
3d-model/m42/零部件1.step
3d-model/OutStpFan/CNC/min-11-bra-connection v164 v1.STEP
3d-model/OutStpFan/3D/m42/YAKE_LED.step
3d-model/OutStpFan/3D/RF_FIX_3MCTR.STEP
3d-model/OutStpFan/3D/3DJoint2 & Joint3_Dummy v164 v1.STEP
3d-model/OutStpFan/3D/3DJoint4_Dummy v164 v2.STEP
3d-model/OutStpFan/3D/3DJoint5_Dummy v164 v2.STEP
3d-model/OutStpFan/3D/3D_1Joint2 & Joint3_Dummy v164 v1.STEP
3d-model/OutStpFan/3D/rfback.step
3d-model/OutStpFan/BACK/35HSH2408-36PG19J-300.SLDPRT
3d-model/OutStpFan/BACK/35HSH2408-36PG19J-300.STEP
3d-model/OutStpFan/BACK/Joint6_Dummy v164 v3.SLDPRT
3d-model/OutStpFan/BACK/Joint6_Dummy v164 v4.SLDPRT
3d-model/OutStpFan/CNC/Joint1_Dummy v164 v1.STEP
3d-model/OutStpFan/CNC/Joint2_Joint3_Dummy v164 v1.STEP
3d-model/OutStpFan/CNC/Joint4_Dummy v164 v1.STEP
3d-model/OutStpFan/CNC/Joint5_Dummy v164 v1.STEP
3d-model/OutStpFan/CNC/Joint6_Dummy v164 v3.STEP
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

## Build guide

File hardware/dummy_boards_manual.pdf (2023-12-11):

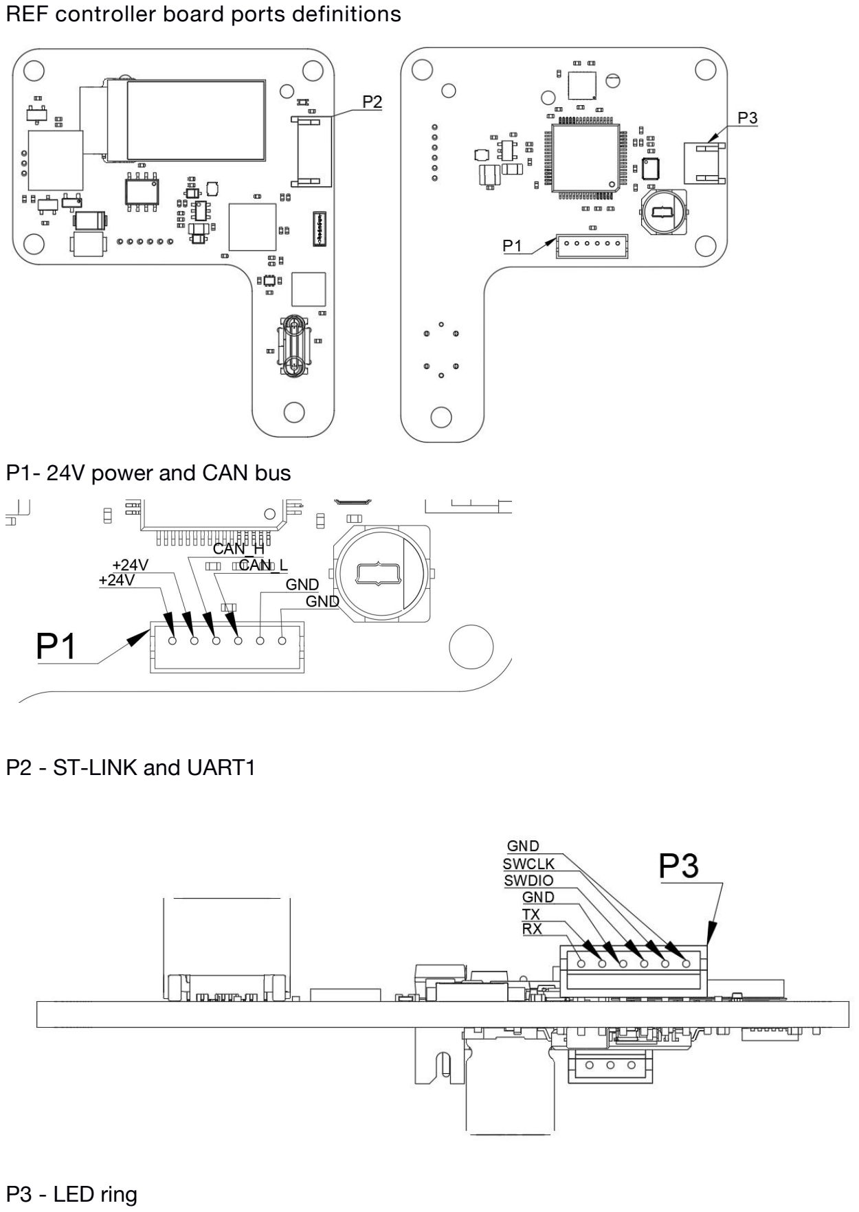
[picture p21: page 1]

REF controller board ports definitions

P1- 24V power and CAN bus

P2 - ST-LINK and UART1

P3 - LED ring

Motor 42 driver board ports definitions

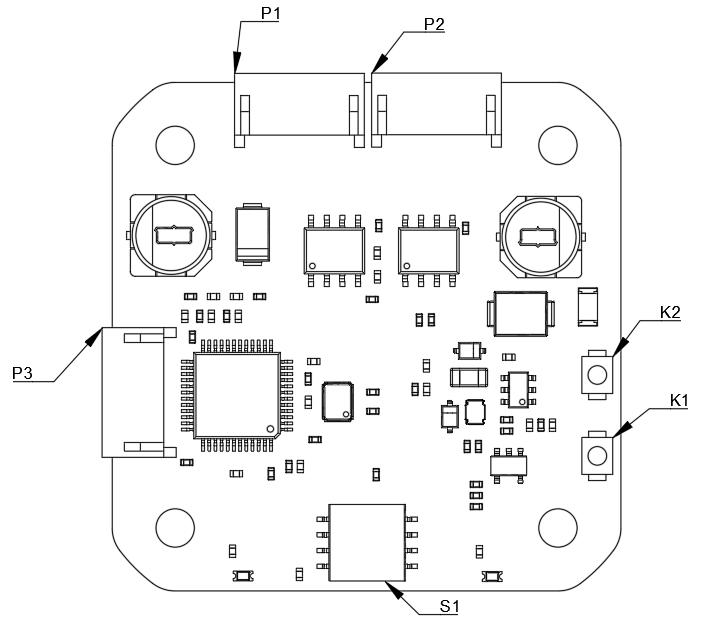
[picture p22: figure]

P1/P2 - 24V power and CAN bus(The below diagram shows P1 and P2 have same pins definition)

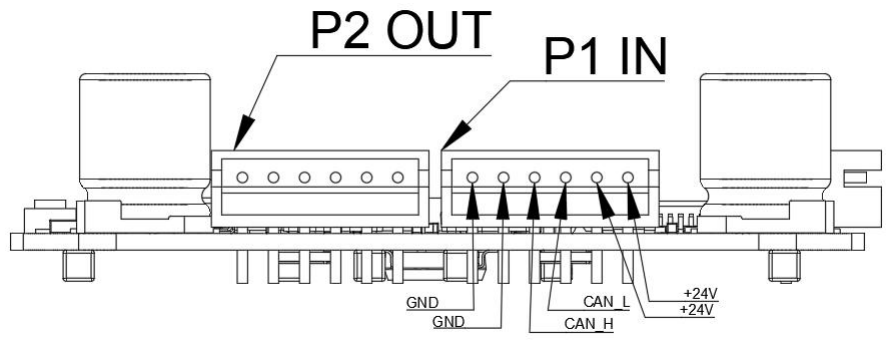
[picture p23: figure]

P3 - ST-LINK and UART1

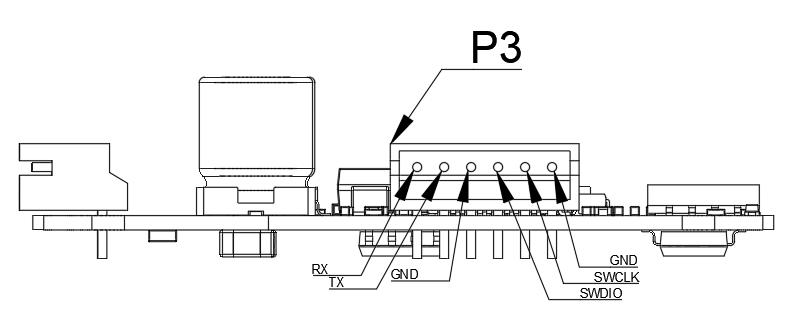
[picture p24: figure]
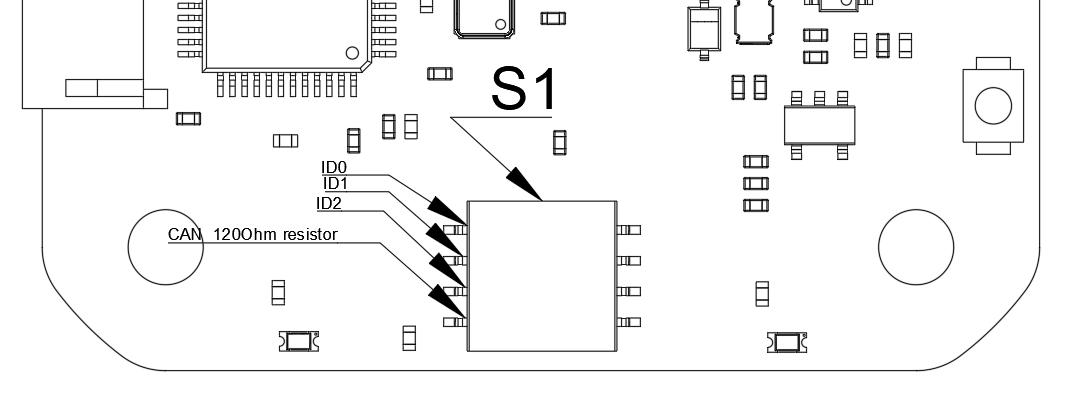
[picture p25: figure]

S1 - Driver board CAN ID definition and terminal resistor

CAN ID definition details

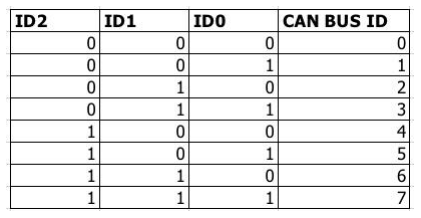
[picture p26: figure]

Motor 35 driver board ports definitions

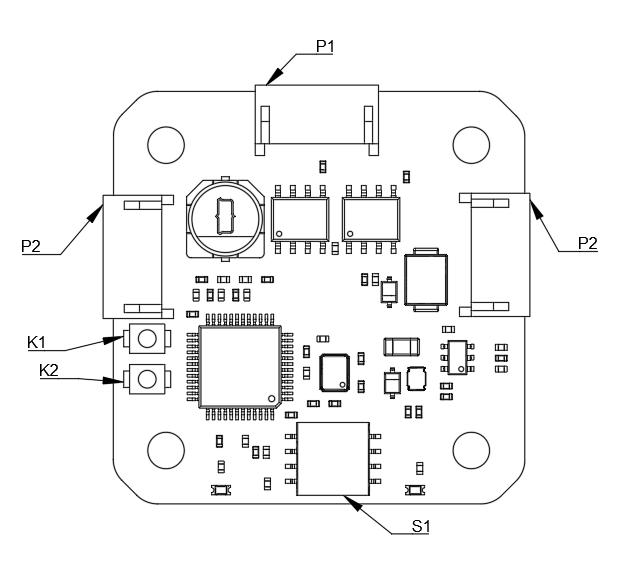
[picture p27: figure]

P1/P2 - 24V power and CAN bus(P1 and P2 share same pins definition with Motor 42 P1 and P2)

P3 - ST-LINK and UART1 (P3 shares same pins definition with Motor 42 P2)

S1 - Driver board CAN ID definition and terminal resistor(S1 shares same pins definition with Motor 42 S1)

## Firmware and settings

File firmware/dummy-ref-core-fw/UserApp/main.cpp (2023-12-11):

#include "common_inc.h"


// On-board Screen, can choose from hi2c2 or hi2c0(soft i2c)
SSD1306 oled(&hi2c0);
// On-board Sensor, used hi2c1
MPU6050 mpu6050(&hi2c1);
// 5 User-Timers, can choose from htim7/htim10/htim11/htim13/htim14
Timer timerCtrlLoop(&htim7, 200);
// 2x2-channel PWMs, used htim9 & htim12, each has 2-channel outputs
PWM pwm(21000, 21000);
// Robot instance
DummyRobot dummy(&hcan1);


/* Thread Definitions -----------------------------------------------------*/
osThreadId_t controlLoopFixUpdateHandle;
void ThreadControlLoopFixUpdate(void* argument)
{
    for (;;)
    {
        // Suspended here until got Notification.
        ulTaskNotifyTake(pdTRUE, portMAX_DELAY);

        if (dummy.IsEnabled())
        {
            // Send control command to Motors & update Joint states
            switch (dummy.commandMode)
            {
                case DummyRobot::COMMAND_TARGET_POINT_SEQUENTIAL:
                case DummyRobot::COMMAND_TARGET_POINT_INTERRUPTABLE:
                case DummyRobot::COMMAND_CONTINUES_TRAJECTORY:
                    dummy.MoveJoints(dummy.targetJoints);
                    dummy.UpdateJointPose6D();
                    break;
                case DummyRobot::COMMAND_MOTOR_TUNING:
                    dummy.tuningHelper.Tick(10);
                    dummy.UpdateJointPose6D();
                    break;
            }
        } else
        {
            // Just update Joint states
            dummy.UpdateJointAngles();
            dummy.UpdateJointPose6D();
        }
    }
}


osThreadId_t ControlLoopUpdateHandle;
void ThreadControlLoopUpdate(void* argument)
{
    for (;;)
    {
        dummy.commandHandler.ParseCommand(dummy.commandHandler.Pop(osWaitForever));
    }
}


osThreadId_t oledTaskHandle;
void ThreadOledUpdate(void* argument)
{
    uint32_t t = micros();
    char buf[16];
    char cmdModeNames[4][4] = {"SEQ", "INT", "TRJ", "TUN"};

    for (;;)
    {
        mpu6050.Update(true);

        oled.clearBuffer();
        oled.setFont(u8g2_font_5x8_tr);
        oled.setCursor(0, 10);
        oled.printf("IMU:%.3f/%.3f", mpu6050.data.ax, mpu6050.data.ay);
        oled.setCursor(85, 10);
        oled.printf("| FPS:%lu", 1000000 / (micros() - t));
        t = micros();

        oled.drawBox(0, 15, 128, 3);
        oled.setCursor(0, 30);
        oled.printf(">%3d|%3d|%3d|%3d|%3d|%3d",
                    (int) roundf(dummy.currentJoints.a[0]), (int) roundf(dummy.currentJoints.a[1]),
                    (int) roundf(dummy.currentJoints.a[2]), (int) roundf(dummy.currentJoints.a[3]),
                    (int) roundf(dummy.currentJoints.a[4]), (int) roundf(dummy.currentJoints.a[5]));

        oled.drawBox(40, 35, 128, 24);
        oled.setFont(u8g2_font_6x12_tr);
        oled.setDrawColor(0);
        oled.setCursor(42, 45);
        oled.printf("%4d|%4d|%4d", (int) roundf(dummy.currentPose6D.X),
                    (int) roundf(dummy.currentPose6D.Y), (int) roundf(dummy.currentPose6D.Z));
        oled.setCursor(42, 56);
        oled.printf("%4d|%4d|%4d", (int) roundf(dummy.currentPose6D.A),
                    (int) roundf(dummy.currentPose6D.B), (int) roundf(dummy.currentPose6D.C));
        oled.setDrawColor(1);
        oled.setCursor(0, 45);
        oled.printf("[XYZ]:");
        oled.setCursor(0, 56);
        oled.printf("[ABC]:");

        oled.setFont(u8g2_font_10x20_tr);
        oled.setCursor(0, 78);
        if (dummy.IsEnabled())
        {
            for (int i = 1; i <= 6; i++)
                buf[i - 1] = (dummy.jointsStateFlag & (1 << i) ? '*' : '_');
            buf[6] = 0;
            oled.printf("[%s] %s", cmdModeNames[dummy.commandMode - 1], buf);
        } else
        {
            oled.printf("[%s] %s", cmdModeNames[dummy.commandMode - 1], "======");
        }

        oled.sendBuffer();
    }
}


/* Timer Callbacks -------------------------------------------------------*/
void OnTimer7Callback()
{
    BaseType_t xHigherPriorityTaskWoken = pdFALSE;

    // Wake & invoke thread IMMEDIATELY.
    vTaskNotifyGiveFromISR(TaskHandle_t(controlLoopFixUpdateHandle), &xHigherPriorityTaskWoken);
    portYIELD_FROM_ISR(xHigherPriorityTaskWoken);
}


/* Default Entry -------------------------------------------------------*/
void Main(void)
{
    // Init all communication staff, including USB-CDC/VCP/UART/CAN etc.
    InitCommunication();

    // Init Robot.
    dummy.Init();

    // Init IMU.
    do
    {
        mpu6050.Init();
        osDelay(100);
    } while (!mpu6050.testConnection());
    mpu6050.InitFilter(200, 100, 50);

    // Init OLED 128x80.
    oled.Init();
    pwm.Start();

    // Init & Run User Threads.
    const osThreadAttr_t controlLoopTask_attributes = {
        .name = "ControlLoopFixUpdateTask",
        .stack_size = 2000,
        .priority = (osPriority_t) osPriorityRealtime,
    };
    controlLoopFixUpdateHandle = osThreadNew(ThreadControlLoopFixUpdate, nullptr,
                                             &controlLoopTask_attributes);

    const osThreadAttr_t ControlLoopUpdateTask_attributes = {
        .name = "ControlLoopUpdateTask",
        .stack_size = 2000,
        .priority = (osPriority_t) osPriorityNormal,
    };
    ControlLoopUpdateHandle = osThreadNew(ThreadControlLoopUpdate, nullptr,
                                          &ControlLoopUpdateTask_attributes);

    const osThreadAttr_t oledTask_attributes = {
        .name = "OledTask",
        .stack_size = 2000,
        .priority = (osPriority_t) osPriorityNormal,   // should >= Normal
    };
    oledTaskHandle = osThreadNew(ThreadOledUpdate, nullptr, &oledTask_attributes);

    // Start Timer Callbacks.
    timerCtrlLoop.SetCallback(OnTimer7Callback);
    timerCtrlLoop.Start();

    // System started, light switch-led up.
    Respond(*uart4StreamOutputPtr, "[sys] Heap remain: %d Bytes\n", xPortGetMinimumEverFreeHeapSize());
    pwm.SetDuty(PWM::CH_A1, 0.5);
}

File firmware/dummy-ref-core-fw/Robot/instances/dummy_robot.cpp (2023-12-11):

#include "communication.hpp"
#include "dummy_robot.h"

inline float AbsMaxOf6(DOF6Kinematic::Joint6D_t _joints, uint8_t &_index)
{
    float max = -1;
    for (uint8_t i = 0; i < 6; i++)
    {
        if (abs(_joints.a[i]) > max)
        {
            max = abs(_joints.a[i]);
            _index = i;
        }
    }

    return max;
}


DummyRobot::DummyRobot(CAN_HandleTypeDef* _hcan) :
    hcan(_hcan)
{
    motorJ[ALL] = new CtrlStepMotor(_hcan, 0, false, 1, -180, 180);
    motorJ[1] = new CtrlStepMotor(_hcan, 1, true, 30, -170, 170);
    motorJ[2] = new CtrlStepMotor(_hcan, 2, false, 30, -73, 90);
    motorJ[3] = new CtrlStepMotor(_hcan, 3, true, 30, 35, 180);
    motorJ[4] = new CtrlStepMotor(_hcan, 4, false, 24, -180, 180);
    motorJ[5] = new CtrlStepMotor(_hcan, 5, true, 30, -120, 120);
    motorJ[6] = new CtrlStepMotor(_hcan, 6, true, 50, -720, 720);
    hand = new DummyHand(_hcan, 7);

    dof6Solver = new DOF6Kinematic(0.109f, 0.035f, 0.146f, 0.115f, 0.052f, 0.072f);
}


DummyRobot::~DummyRobot()
{
    for (int j = 0; j <= 6; j++)
        delete motorJ[j];

    delete hand;
    delete dof6Solver;
}


void DummyRobot::Init()
{
    SetCommandMode(DEFAULT_COMMAND_MODE);
    SetJointSpeed(DEFAULT_JOINT_SPEED);
}


void DummyRobot::Reboot()
{
    motorJ[ALL]->Reboot();
    osDelay(500); // waiting for all joints done
    HAL_NVIC_SystemReset();
}


void DummyRobot::MoveJoints(DOF6Kinematic::Joint6D_t _joints)
{
    for (int j = 1; j <= 6; j++)
    {
        motorJ[j]->SetAngleWithVelocityLimit(_joints.a[j - 1] - initPose.a[j - 1],
                                             dynamicJointSpeeds.a[j - 1]);
    }
}


bool DummyRobot::MoveJ(float _j1, float _j2, float _j3, float _j4, float _j5, float _j6)
{
    DOF6Kinematic::Joint6D_t targetJointsTmp(_j1, _j2, _j3, _j4, _j5, _j6);
    bool valid = true;

    for (int j = 1; j <= 6; j++)
    {
        if (targetJointsTmp.a[j - 1] > motorJ[j]->angleLimitMax ||
            targetJointsTmp.a[j - 1] < motorJ[j]->angleLimitMin)
            valid = false;
    }

    if (valid)
    {
        DOF6Kinematic::Joint6D_t deltaJoints = targetJointsTmp - currentJoints;
        uint8_t index;
        float maxAngle = AbsMaxOf6(deltaJoints, index);
        float time = maxAngle * (float) (motorJ[index + 1]->reduction) / jointSpeed;
        for (int j = 1; j <= 6; j++)
        {
            dynamicJointSpeeds.a[j - 1] =
                abs(deltaJoints.a[j - 1] * (float) (motorJ[j]->reduction) / time * 0.1f); //0~10r/s
        }

        jointsStateFlag = 0;
        targetJoints = targetJointsTmp;

        return true;
    }

    return false;
}


bool DummyRobot::MoveL(float _x, float _y, float _z, float _a, float _b, float _c)
{
    DOF6Kinematic::Pose6D_t pose6D(_x, _y, _z, _a, _b, _c);
    DOF6Kinematic::IKSolves_t ikSolves{};
    DOF6Kinematic::Joint6D_t lastJoint6D{};

    dof6Solver->SolveIK(pose6D, lastJoint6D, ikSolves);

    bool valid[8];
    int validCnt = 0;

    for (int i = 0; i < 8; i++)
    {
        valid[i] = true;

        for (int j = 1; j <= 6; j++)
        {
            if (ikSolves.config[i].a[j - 1] > motorJ[j]->angleLimitMax ||
                ikSolves.config[i].a[j - 1] < motorJ[j]->angleLimitMin)
            {
                valid[i] = false;
                continue;
            }
        }

        if (valid[i]) validCnt++;
    }

    if (validCnt)
    {
        float min = 1000;
        uint8_t indexConfig = 0, indexJoint = 0;
        for (int i = 0; i < 8; i++)
        {
            if (valid[i])
            {
                for (int j = 0; j < 6; j++)
                    lastJoint6D.a[j] = ikSolves.config[i].a[j];
                DOF6Kinematic::Joint6D_t tmp = currentJoints - lastJoint6D;
                float maxAngle = AbsMaxOf6(tmp, indexJoint);
                if (maxAngle < min)
                {
                    min = maxAngle;
                    indexConfig = i;
                }
            }
        }

        return MoveJ(ikSolves.config[indexConfig].a[0], ikSolves.config[indexConfig].a[1],
                     ikSolves.config[indexConfig].a[2], ikSolves.config[indexConfig].a[3],
                     ikSolves.config[indexConfig].a[4], ikSolves.config[indexConfig].a[5]);
    }

    return false;
}

void DummyRobot::UpdateJointAngles()
{
    motorJ[ALL]->UpdateAngle();
}


void DummyRobot::UpdateJointAnglesCallback()
{
    for (int i = 1; i <= 6; i++)
    {
        currentJoints.a[i - 1] = motorJ[i]->angle + initPose.a[i - 1];

        if (motorJ[i]->state == CtrlStepMotor::FINISH)
            jointsStateFlag |= (1 << i);
        else
            jointsStateFlag &= ~(1 << i);
    }
}


void DummyRobot::SetJointSpeed(float _speed)
{
    if (_speed < 0)_speed = 0;
    else if (_speed > 100) _speed = 100;

    jointSpeed = _speed * jointSpeedRatio;
}


void DummyRobot::SetJointAcceleration(float _acc)
{
    if (_acc < 0)_acc = 0;
    else if (_acc > 100) _acc = 100;

    for (int i = 1; i <= 6; i++)
        motorJ[i]->SetAcceleration(_acc / 100 * DEFAULT_JOINT_ACCELERATION_BASES.a[i - 1]);
}


void DummyRobot::CalibrateHomeOffset()
{
    // Disable FixUpdate, but not disable motors
    isEnabled = false;
    motorJ[ALL]->SetEnable(true);

    // 1.Manually move joints to L-Pose [precisely]
    // ...
    motorJ[2]->SetCurrentLimit(0.5);
    motorJ[3]->SetCurrentLimit(0.5);
    osDelay(500);

    // 2.Apply Home-Offset the first time
    motorJ[ALL]->ApplyPositionAsHome();
    osDelay(500);

    // 3.Go to Resting-Pose
    initPose = DOF6Kinematic::Joint6D_t(0, 0, 90, 0, 0, 0);
    currentJoints = DOF6Kinematic::Joint6D_t(0, 0, 90, 0, 0, 0);
    Resting();
    osDelay(500);

    // 4.Apply Home-Offset the second time
    motorJ[ALL]->ApplyPositionAsHome();
    osDelay(500);
    motorJ[2]->SetCurrentLimit(1);
    motorJ[3]->SetCurrentLimit(1);
    osDelay(500);

    Reboot();
}


void DummyRobot::Homing()
{
    float lastSpeed = jointSpeed;
    SetJointSpeed(10);

    MoveJ(0, 0, 90, 0, 0, 0);
    MoveJoints(targetJoints);
    while (IsMoving())
        osDelay(10);

    SetJointSpeed(lastSpeed);
}


void DummyRobot::Resting()
{
    float lastSpeed = jointSpeed;
    SetJointSpeed(10);

    MoveJ(REST_POSE.a[0], REST_POSE.a[1], REST_POSE.a[2],
          REST_POSE.a[3], REST_POSE.a[4], REST_POSE.a[5]);
    MoveJoints(targetJoints);
    while (IsMoving())
        osDelay(10);

    SetJointSpeed(lastSpeed);
}


void DummyRobot::SetEnable(bool _enable)
{
    motorJ[ALL]->SetEnable(_enable);
    isEnabled = _enable;
}


void DummyRobot::UpdateJointPose6D()
{
    dof6Solver->SolveFK(currentJoints, currentPose6D);
    currentPose6D.X *= 1000; // m -> mm
    currentPose6D.Y *= 1000; // m -> mm
    currentPose6D.Z *= 1000; // m -> mm
}


bool DummyRobot::IsMoving()
{
    return jointsStateFlag != 0b1111110;
}


bool DummyRobot::IsEnabled()
{
    return isEnabled;
}
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

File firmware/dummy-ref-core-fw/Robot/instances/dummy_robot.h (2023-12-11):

#ifndef REF_STM32F4_FW_DUMMY_ROBOT_H
#define REF_STM32F4_FW_DUMMY_ROBOT_H

#include "algorithms/kinematic/6dof_kinematic.h"
#include "actuators/ctrl_step/ctrl_step.hpp"
#include "string"
#define ALL 0

/*
  |   PARAMS   | `current_limit` | `acceleration` | `dce_kp` | `dce_kv` | `dce_ki` | `dce_kd` |
  | ---------- | --------------- | -------------- | -------- | -------- | -------- | -------- |
  | **Joint1** | 2               | 30             | 1000     | 80       | 200      | 250      |
  | **Joint2** | 2               | 30             | 1000     | 80       | 200      | 200      |
  | **Joint3** | 2               | 30             | 1500     | 80       | 200      | 250      |
  | **Joint4** | 2               | 30             | 1000     | 80       | 200      | 250      |
  | **Joint5** | 2               | 30             | 1000     | 80       | 200      | 250      |
  | **Joint6** | 2               | 30             | 1000     | 80       | 200      | 250      |
 */


class DummyHand
{
public:
    uint8_t nodeID = 7;
    float maxCurrent = 0.7;


    DummyHand(CAN_HandleTypeDef* _hcan, uint8_t _id);


    void SetAngle(float _angle);
    void SetMaxCurrent(float _val);
    void SetEnable(bool _enable);


    // Communication protocol definitions
    auto MakeProtocolDefinitions()
    {
        return make_protocol_member_list(
            make_protocol_function("set_angle", *this, &DummyHand::SetAngle, "angle"),
            make_protocol_function("set_enable", *this, &DummyHand::SetEnable, "enable"),
            make_protocol_function("set_current_limit", *this, &DummyHand::SetMaxCurrent, "current")
        );
    }


private:
    CAN_HandleTypeDef* hcan;
    uint8_t canBuf[8];
    CAN_TxHeaderTypeDef txHeader;
    float minAngle = 0;
    float maxAngle = 45;
};


class DummyRobot
{
public:
    explicit DummyRobot(CAN_HandleTypeDef* _hcan);
    ~DummyRobot();


    enum CommandMode
    {
        COMMAND_TARGET_POINT_SEQUENTIAL = 1,
        COMMAND_TARGET_POINT_INTERRUPTABLE,
        COMMAND_CONTINUES_TRAJECTORY,
        COMMAND_MOTOR_TUNING
    };


    class TuningHelper
    {
    public:
        explicit TuningHelper(DummyRobot* _context) : context(_context)
        {
        }

        void SetTuningFlag(uint8_t _flag);
        void Tick(uint32_t _timeMillis);
        void SetFreqAndAmp(float _freq, float _amp);


        // Communication protocol definitions
        auto MakeProtocolDefinitions()
        {
            return make_protocol_member_list(
                make_protocol_function("set_tuning_freq_amp", *this,
                                       &TuningHelper::SetFreqAndAmp, "freq", "amp"),
                make_protocol_function("set_tuning_flag", *this,
                                       &TuningHelper::SetTuningFlag, "flag")
            );
        }


    private:
        DummyRobot* context;
        float time = 0;
        uint8_t tuningFlag = 0;
        float frequency = 1;
        float amplitude = 1;
    };
    TuningHelper tuningHelper = TuningHelper(this);


    // This is the pose when power on.
    const DOF6Kinematic::Joint6D_t REST_POSE = {0, -73, 180, 0, 0, 0};
    const float DEFAULT_JOINT_SPEED = 30;  // degree/s
    const DOF6Kinematic::Joint6D_t DEFAULT_JOINT_ACCELERATION_BASES = {150, 100, 200, 200, 200, 200};
    const float DEFAULT_JOINT_ACCELERATION_LOW = 30;    // 0~100
    const float DEFAULT_JOINT_ACCELERATION_HIGH = 100;  // 0~100
    const CommandMode DEFAULT_COMMAND_MODE = COMMAND_TARGET_POINT_INTERRUPTABLE;


    DOF6Kinematic::Joint6D_t currentJoints = REST_POSE;
    DOF6Kinematic::Joint6D_t targetJoints = REST_POSE;
    DOF6Kinematic::Joint6D_t initPose = REST_POSE;
    DOF6Kinematic::Pose6D_t currentPose6D = {};
    volatile uint8_t jointsStateFlag = 0b00000000;
    CommandMode commandMode = DEFAULT_COMMAND_MODE;
    CtrlStepMotor* motorJ[7] = {nullptr};
    DummyHand* hand = {nullptr};


    void Init();
    bool MoveJ(float _j1, float _j2, float _j3, float _j4, float _j5, float _j6);
    bool MoveL(float _x, float _y, float _z, float _a, float _b, float _c);
    void MoveJoints(DOF6Kinematic::Joint6D_t _joints);
    void SetJointSpeed(float _speed);
    void SetJointAcceleration(float _acc);
    void UpdateJointAngles();
    void UpdateJointAnglesCallback();
    void UpdateJointPose6D();
    void Reboot();
    void SetEnable(bool _enable);
    void CalibrateHomeOffset();
    void Homing();
    void Resting();
    bool IsMoving();
    bool IsEnabled();
    void SetCommandMode(uint32_t _mode);


    // Communication protocol definitions
    auto MakeProtocolDefinitions()
    {
        return make_protocol_member_list(
            make_protocol_function("calibrate_home_offset", *this, &DummyRobot::CalibrateHomeOffset),
            make_protocol_function("homing", *this, &DummyRobot::Homing),
            make_protocol_function("resting", *this, &DummyRobot::Resting),
            make_protocol_object("joint_1", motorJ[1]->MakeProtocolDefinitions()),
            make_protocol_object("joint_2", motorJ[2]->MakeProtocolDefinitions()),
            make_protocol_object("joint_3", motorJ[3]->MakeProtocolDefinitions()),
            make_protocol_object("joint_4", motorJ[4]->MakeProtocolDefinitions()),
            make_protocol_object("joint_5", motorJ[5]->MakeProtocolDefinitions()),
            make_protocol_object("joint_6", motorJ[6]->MakeProtocolDefinitions()),
            make_protocol_object("joint_all", motorJ[ALL]->MakeProtocolDefinitions()),
            make_protocol_object("hand", hand->MakeProtocolDefinitions()),
            make_protocol_function("reboot", *this, &DummyRobot::Reboot),
            make_protocol_function("set_enable", *this, &DummyRobot::SetEnable, "enable"),
            make_protocol_function("move_j", *this, &DummyRobot::MoveJ, "j1", "j2", "j3", "j4", "j5", "j6"),
            make_protocol_function("move_l", *this, &DummyRobot::MoveL, "x", "y", "z", "a", "b", "c"),
            make_protocol_function("set_joint_speed", *this, &DummyRobot::SetJointSpeed, "speed"),
            make_protocol_function("set_joint_acc", *this, &DummyRobot::SetJointAcceleration, "acc"),
            make_protocol_function("set_command_mode", *this, &DummyRobot::SetCommandMode, "mode"),
            make_protocol_object("tuning", tuningHelper.MakeProtocolDefinitions())
        );
    }


    class CommandHandler
    {
    public:
        explicit CommandHandler(DummyRobot* _context) : context(_context)
        {
            commandFifo = osMessageQueueNew(16, 64, nullptr);
        }

        uint32_t Push(const std::string &_cmd);
        std::string Pop(uint32_t timeout);
        uint32_t ParseCommand(const std::string &_cmd);
        uint32_t GetSpace();
        void ClearFifo();
        void EmergencyStop();


    private:
        DummyRobot* context;
        osMessageQueueId_t commandFifo;
        char strBuffer[64]{};
    };
    CommandHandler commandHandler = CommandHandler(this);
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

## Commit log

2023-12-11 add pcb designs.zip
2023-12-22 fix rf board 3d and fix 42 boot 3d
    [3DJoint4_Dummy v164 v3.SLDPRT, 3DJoint5_Dummy v164 v2.SLDPRT, 3dJoint4_Dummy v164 v1.SLDPRT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]
